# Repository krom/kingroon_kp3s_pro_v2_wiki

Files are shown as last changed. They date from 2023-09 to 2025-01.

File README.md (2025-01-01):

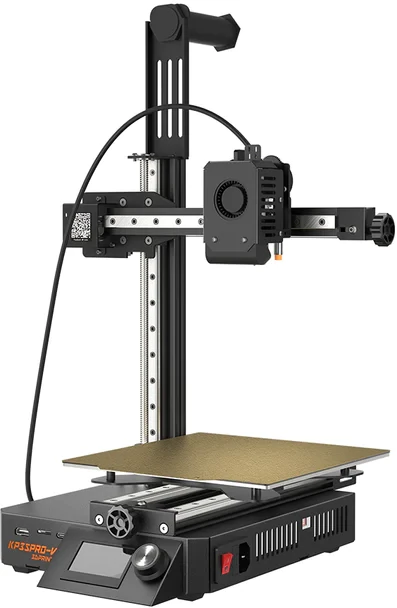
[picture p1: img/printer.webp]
Printer

# База знаний по принтеру Kingroon KP3S Pro V2 [RU]

* [Мануалы](manuals)
  * [SSH доступ](manuals/ssh_ru.md)
  * [Настройка wifi на принтере](manuals/wifi_connection_setup.md)
  * [Подключение к принтеру через сериальную консоль](manuals/serial_console_connection_ru.md)
  * [Обновление версии fluidd](manuals/fluidd_update_ru.md)
* [Известные проблемы](known_issues)
  * [Пластиковые проставки под платой на голове](known_issues/MKS_THR_Spacers_ru.md)
  * [Недостаточно затянутое сопло](known_issues/Nozzle_not_tight_ru.md) 
  * [Торчащие внутри балки X винты](known_issues/stick_out_screws_in_bolster_ru.md)
  * [Штатная улитка обдува не регулирует мощность](known_issues/Blowing_power_cannot_be_ajusted_ru.md)
  * [Проблема с упором головы по оси X](known_issues/x_offset_ru.md)
  * [Перевернутая скоба натяжителя ремня](known_issues/Inverted_tensioner_bracket_ru.md)
  * [Неправильные настройки шагов экструдера](known_issues/rotation_distance_ru.md)
  * [Не отображается карта стола](known_issues/fluidd_not_show_mesh_ru.md)
* [Советы по печати](tips)
  * [Клей](tips/Printing_glue_ru.md)
* [Апгрейд](upgrade)
  * [Улитка обдува](upgrade/Blower_ru.md)
  * [Хитблок от CHC](upgrade/CHC_ru.md)
  * [Установка датчика окончания филамента](upgrade/filament_runout_sensor_ru.md)
  * [Направляющая для кабеля стола](upgrade/bed_cable_guide_ru.md)
  * [Проставка между двигателем и фидером](upgrade/spacer_between_motor_and_feeder_ru.md)
* [Ремонт](repair)
  * [Прошивка платы головы из принтера](repair/How_to_flash_THR_Board_from_printer_ru.md)

# Kingroon KP3S Pro V2 Wiki [EN]
* [Manauls](manuals)
* [Known issues](known_issues)
  * [Nozzle is not tight](known_issues/Nozzle_not_tight_en.md) 
* [Tips and tricks](tips)
* [Upgrade](upgrade)
  * [Enable Filament Run Out Detection](upgrade/filament_runout_sensor_en.md)
* [Repair](repair)

----
[Группа в Telegram](https://t.me/kingroon_printers/384212)

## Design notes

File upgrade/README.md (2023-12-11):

# Апгрейд [RU]
* [Улитка](Blower_ru.md)
* [Хитблок от CHC](CHC_ru.md)
* [Установка датчика окончания филамента](filament_runout_sensor_ru.md)
* [Направляющая для кабеля стола](bed_cable_guide_ru.md)
* [Проставка между двигателем и фидером](spacer_between_motor_and_feeder_ru.md)
* [Замена заводской антенны WLAN](wlan_antenna.md)

# Upgrade [EN]
* [Enable Filament Run Out Detection](./filament_runout_sensor_en.md)

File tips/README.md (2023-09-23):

# Советы по печати
* [Клей](Printing_glue_ru.md)

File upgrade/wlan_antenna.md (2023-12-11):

## Замена антенны WLAN

Заводская антенна WLAN (она-же WI-FI) на принтере имеет довольно слабый прием. Дело в том, что ее реализовали в виде наклейки (та, которая с названием модели) на металлическом корпусе.
Близость металлического корпуса не способствует качеству приема:
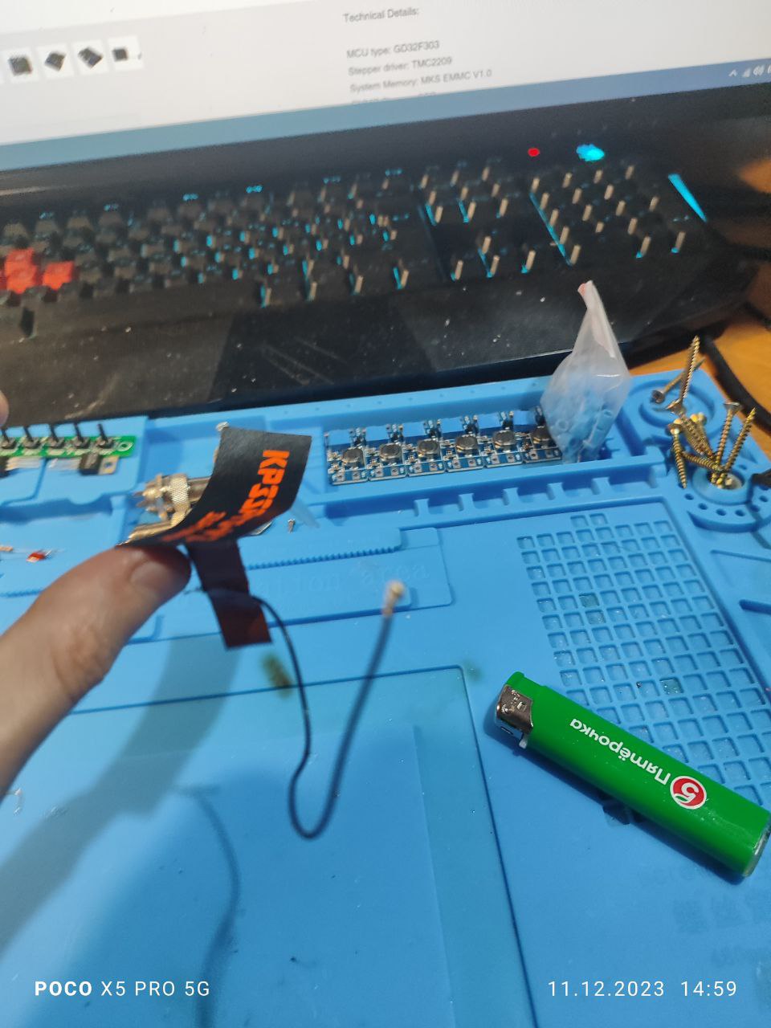
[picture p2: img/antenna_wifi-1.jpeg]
заводская антенна

Поскольку антенна подключена через стандартный разьем типа IPEX, можно заменить ее на что-то более чуствительное, например на внешнюю антенну от ESP32 типа такой:
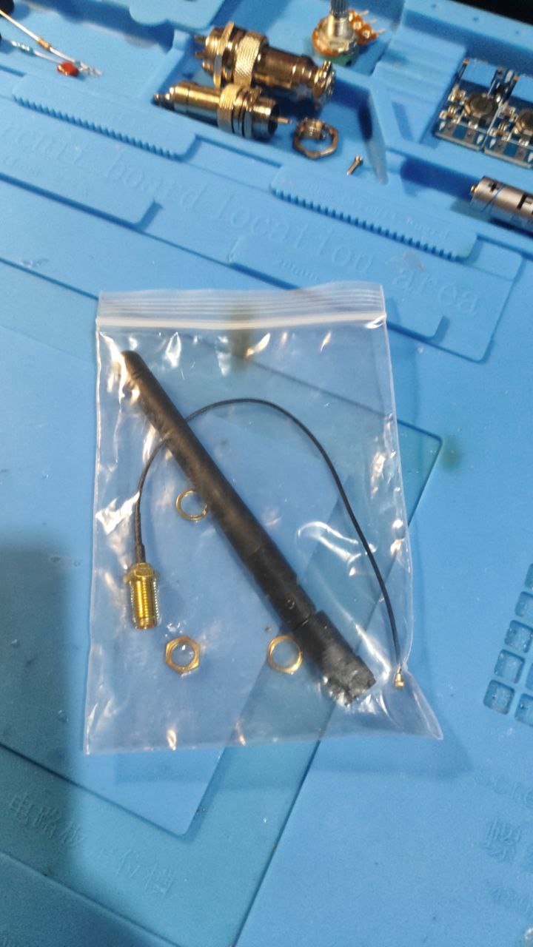
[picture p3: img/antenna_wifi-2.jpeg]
антенна ESP

Нужна антенна поддерживающая 2.4 Mhz и имеющая разьем [типа IPEX](https://en.wikipedia.org/wiki/Hirose_U.FL)
Т.е. отдираем наклейку - под ней стандартное круглое отверстие, через которое проходит кабель антенны к плате 
Отключаем старую антенну, заменяем на новую и перестаем мучаться, что принтер постоянно теряет связь с вашим домашним роутером:
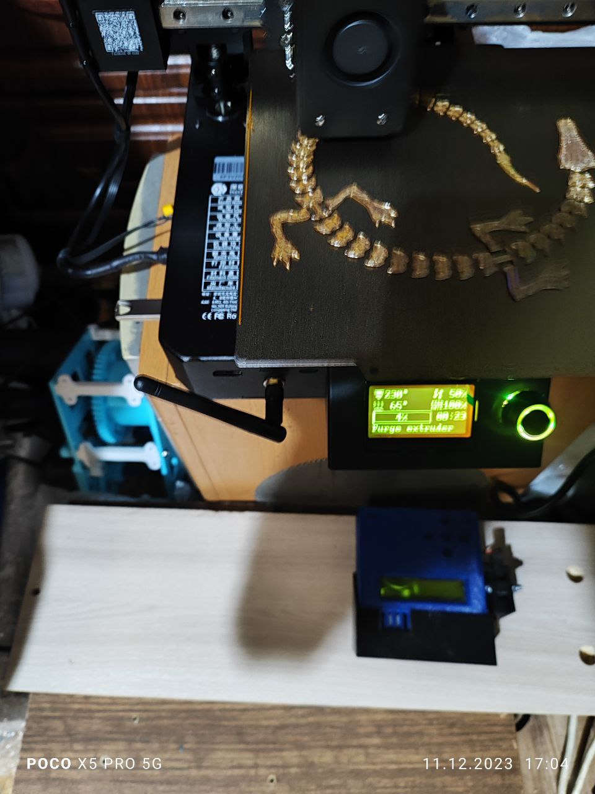
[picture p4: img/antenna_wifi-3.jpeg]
новая антенна


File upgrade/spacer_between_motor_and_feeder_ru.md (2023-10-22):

# Проставка между мотором и фидером

Шестерня двигателя не полностью пересекается с шестерней фидера и последняя может быстрее изнашиваться

Рекомендуется распечатать и установить проставку для выравнивания шестерней

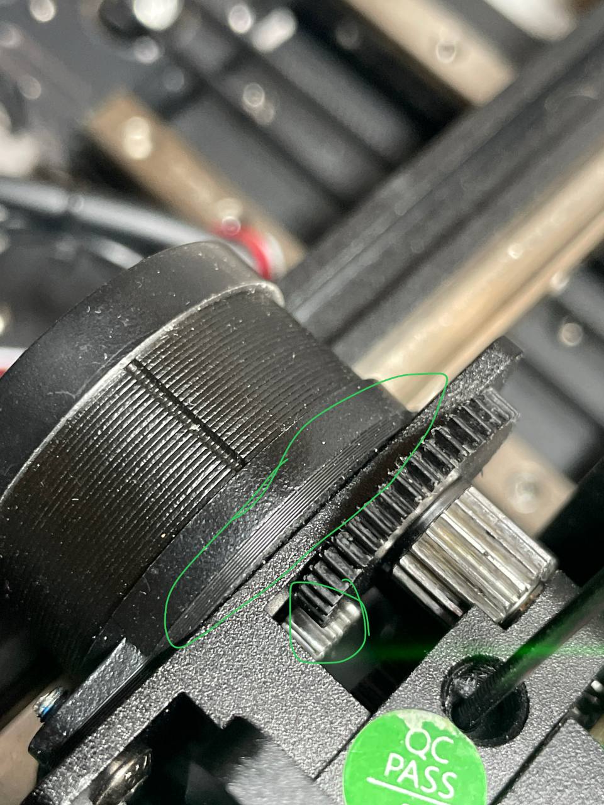
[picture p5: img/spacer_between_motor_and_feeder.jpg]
Spacer


## Доработка

1. Скачать [файл проставки с Printables](https://www.printables.com/model/566505-nema-14-junta-kp3s-pro-v2)
2. Распечатать деталь из PLA, лучше PETG
3. Открутить 2 винта крепления двигателя (для удобства лучше снять кожух головы)
4. Установить проставку как показано на изображении выше
5. Собрать голову в обратном порядке

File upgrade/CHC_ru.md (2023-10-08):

# Установка CHC или CHC pro

## Первые ревизии

В зависимости от того какая ревизия принтера у вас, стоковый хитблок можно заменить на более качественный от CHC/CHC Pro от Trianglelab

#### На версию с экраном под стоковый обдув подходит [CHC](https://alii.pub/6smfm6)

<div style="width: 60%; height: 60%">

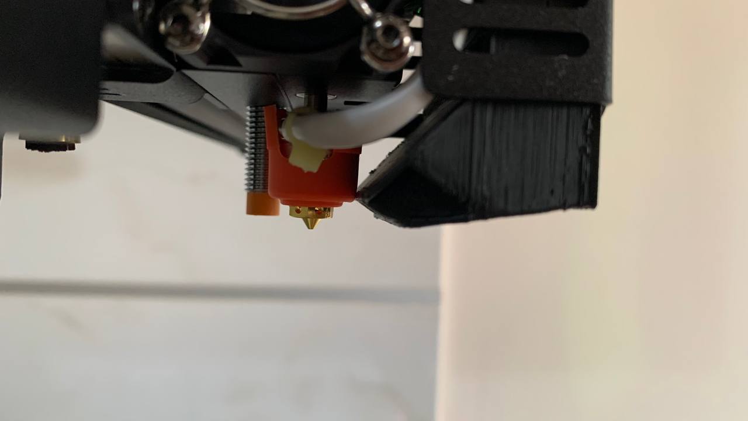
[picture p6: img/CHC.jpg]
CHC


</div>

#### На версию без экрана под стоковый обдув подходит [CHC Pro](https://alii.pub/6smfmk)

<div style="width: 60%; height: 60%">

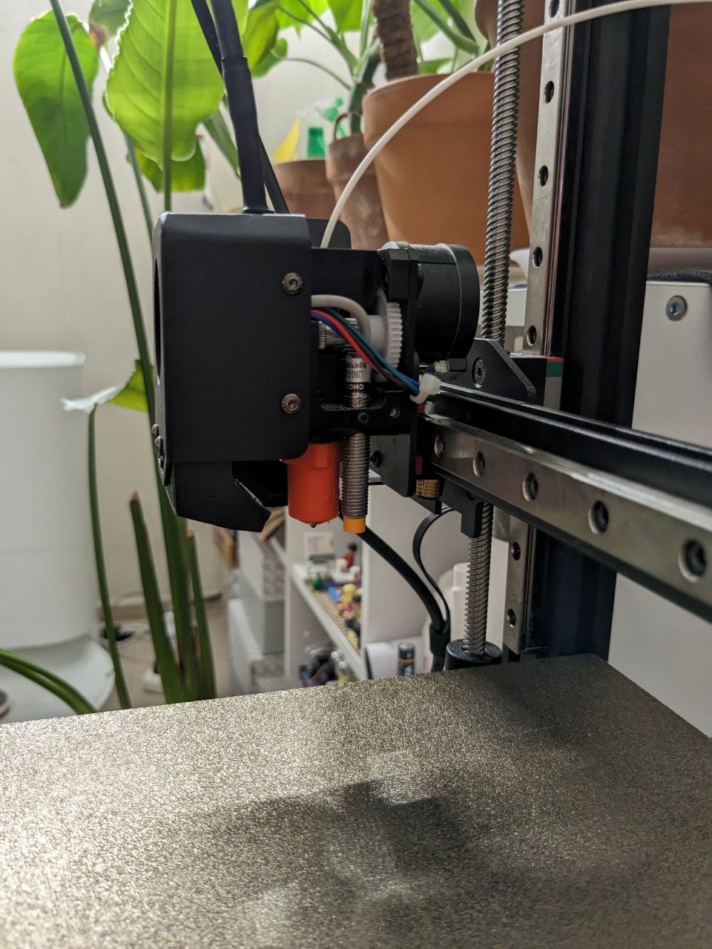
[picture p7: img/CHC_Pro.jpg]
CHC Pro


</div>

В обоих случаях используется горло длинной 25 мм, можно использовать либо стоковое, либо
* от [V5 ANYCUBIC Vyper](https://alii.pub/6sksir) - Если у вас **6 мм горло** и версия принтера без экранчика
* от [3DSWAY V6](https://alii.pub/6skskb) - Если у вас **7 мм горло** и версия принтера с экранчиком

> Проверяйте заранее диаметр горла перед тем как заказывать замену

## Более новые ревизии

В последних ревизиях принтера конструкция хитблока значительно изменилась. Теперь хитблок и горло составляют единое целое. В этих ревизиях заменить хитблок на CHC не представляется возможным

<div style="width: 60%; height: 60%">

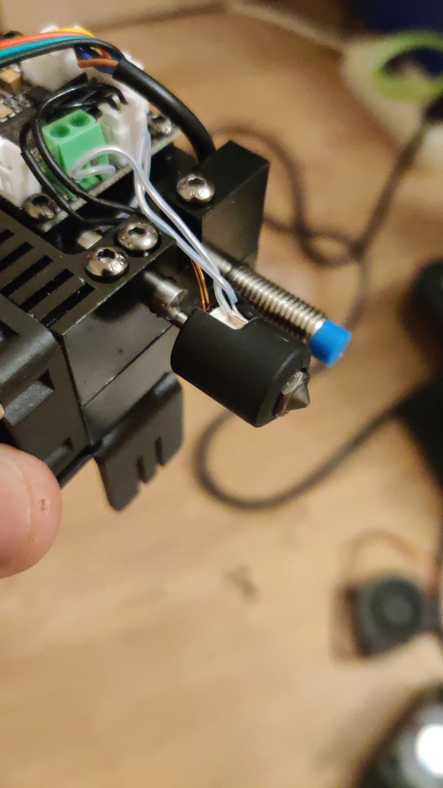
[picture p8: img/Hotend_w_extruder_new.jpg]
Hotend_w_extruder_new


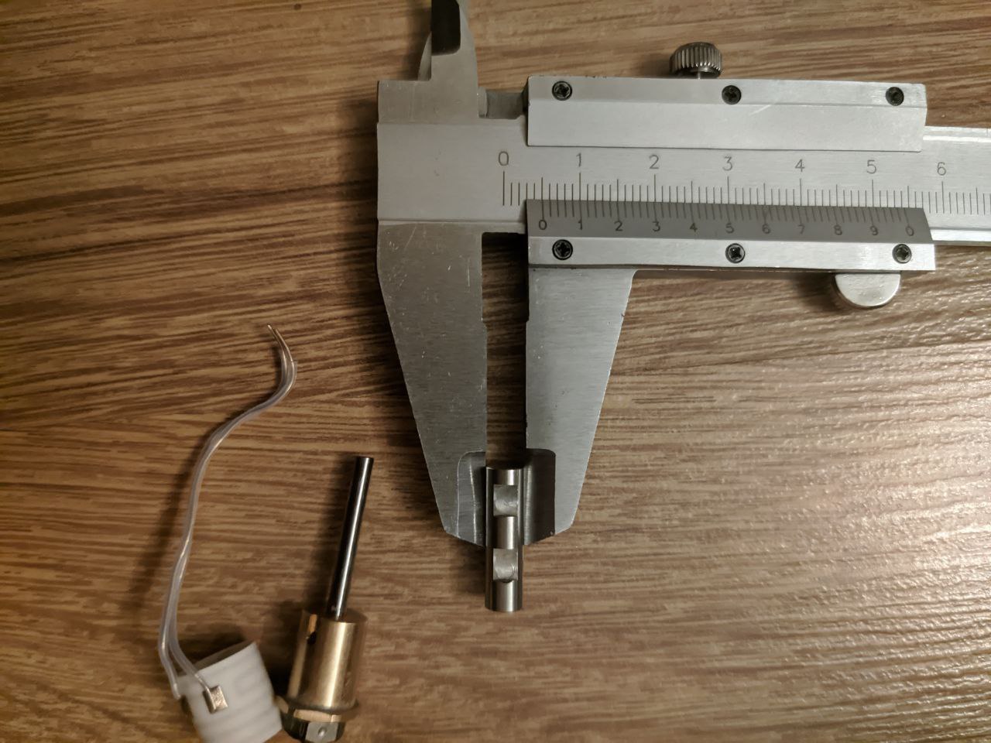
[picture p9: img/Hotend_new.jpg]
Hotend_new


</div>

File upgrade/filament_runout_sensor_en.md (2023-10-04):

# Enable Filament Run Out Detection

> Original post [here](https://kingroon.com/blogs/3d-print-101/enable-filament-run-out-detection-on-your-kingroon-kp3s-pro-v2-in-5-minutes)

The printer does not have a filament end sensor out of box, however, it can be easily installed separately

## Step 1
First you need to purchase the Ender 3 CR10 3D Printer Filament Break Detection Module

* [Official website](https://kingroon.com/products/3d-printer-filament-detection-sensor)
* [AliExpress](https://alii.pub/6sjr66)

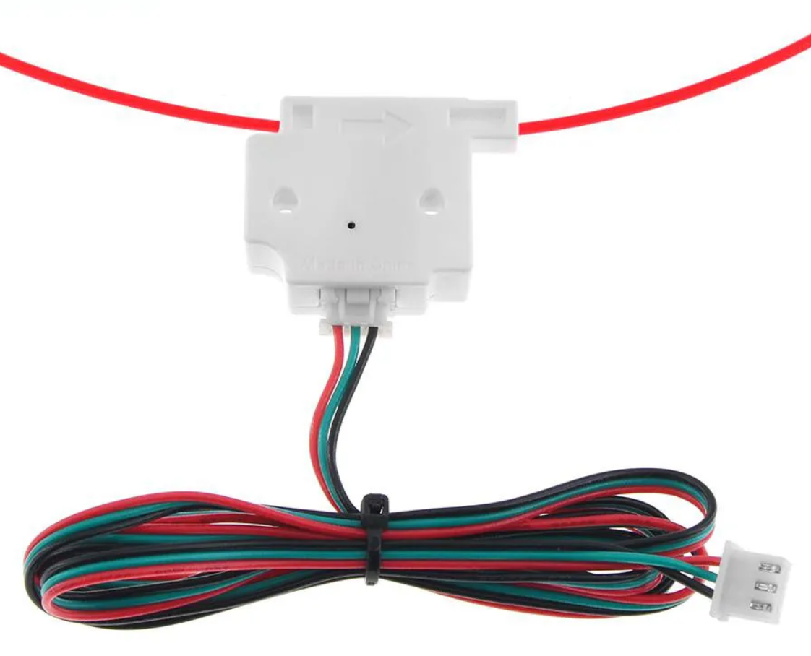
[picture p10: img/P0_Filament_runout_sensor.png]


## Step 2
Turn off the printer, remove the bottom cover then connect the filament run out sensor to the **PA1** port.

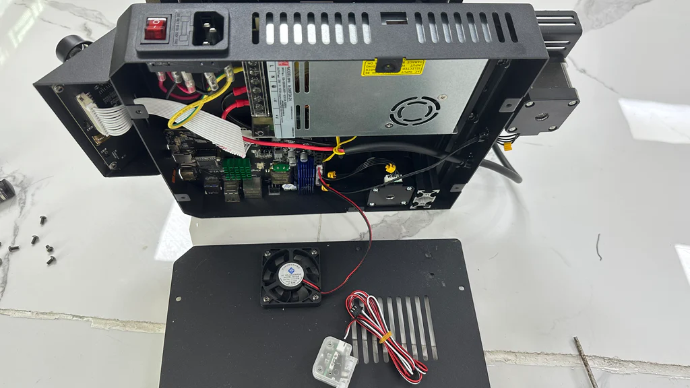
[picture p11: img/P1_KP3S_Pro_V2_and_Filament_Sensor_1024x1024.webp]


Go to the Y-axis motor, put the cable in through the hole near it.

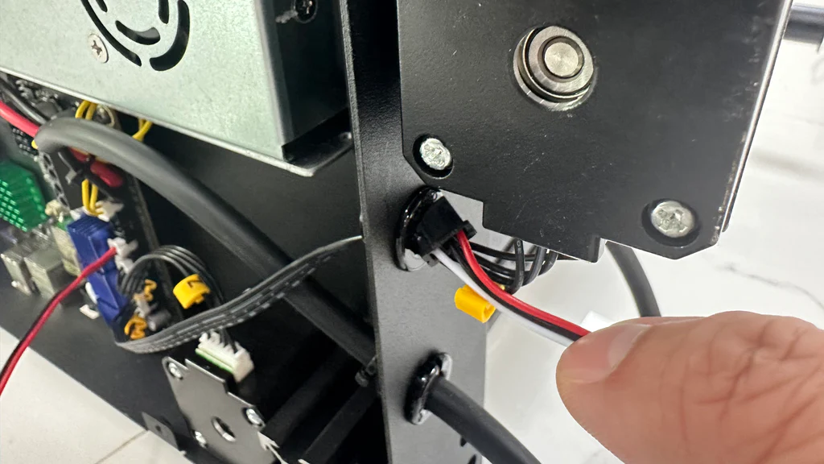
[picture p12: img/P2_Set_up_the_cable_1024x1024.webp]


Then connect the it to the **PA1** port and use some zip to fix it.

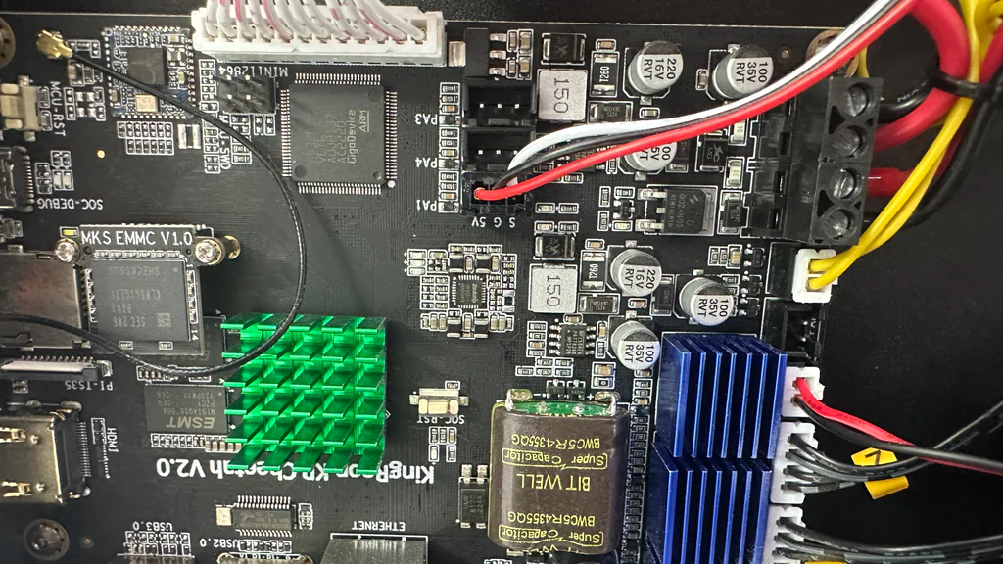
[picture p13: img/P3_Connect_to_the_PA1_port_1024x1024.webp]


After that you can put everything back and arrange the cables.
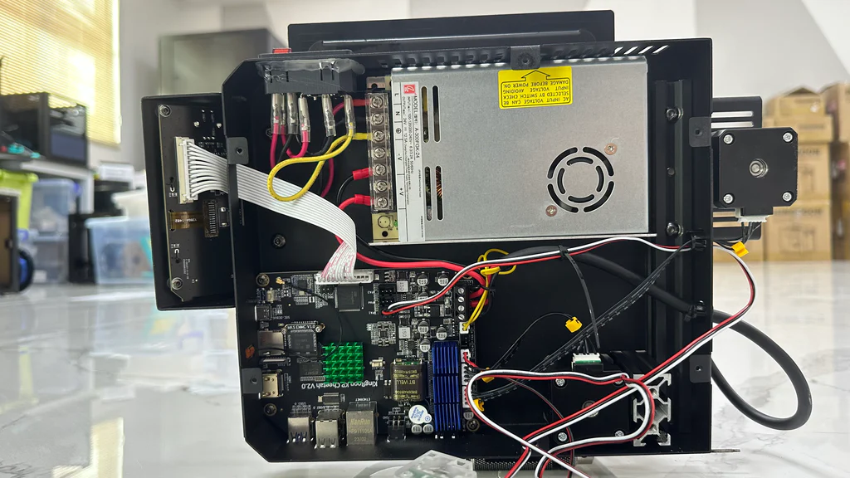
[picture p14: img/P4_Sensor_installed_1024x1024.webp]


## Step 3

Arrange the cables and install the sensor. The filament sensor has a cable that is over 1 meter, you need to fix it with the current ones to make it won’t cause any troubles.

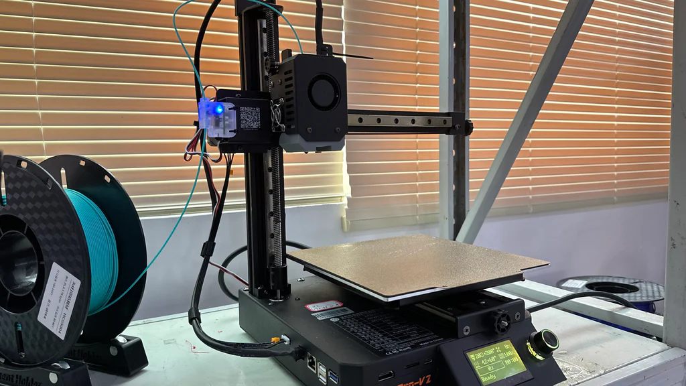
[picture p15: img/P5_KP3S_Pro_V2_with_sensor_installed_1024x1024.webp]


Then you can install the filament sensor with screws on the left side, like a KP3S Pro S1, or at the top of Z-axis. For the second way, you better get one print to make the filament guide smoothly. Since the KP3S Pro V2 prints in high speed, fixing it with ZIP won’t be enough.

Once you turn on the printer and insert the filament, the sensor should be on blue light. So, when the filament runs out on your KP3S Pro V2, the printing will be paused. After adding the filament, you can go the Klipper dashboard to resume it.

Since it is Klipper and our system images are updating, the resume printing might be automagical soon.

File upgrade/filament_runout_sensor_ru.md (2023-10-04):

# Установка датчика окончания филамента

> Оригинал статьи [тут](https://kingroon.com/blogs/3d-print-101/enable-filament-run-out-detection-on-your-kingroon-kp3s-pro-v2-in-5-minutes)

Принтер, не имеет датчика окончания филамента, однако, его можно легко установить отдельно

## Шаг 1
Для начала нужно приобрести Модуль обнаружения разрыва нити 3D-принтера Ender 3 CR10

* [Официальный сайт](https://kingroon.com/products/3d-printer-filament-detection-sensor)
* [AliExpress](https://alii.pub/6sjr66)



## Шаг 2
Выключите принтер, снимите нижнюю крышку, затем подключите датчик окончания нити к порту **PA1**



Ввод кабеля оптимальнее выполнить около мотора оси Y, проденьте кабель через отверстие возле него.



Затем подключите его к порту **PA1** и зафиксируйте с помощью пластиковой стяжки.



После этого можно собирать все обратно и подключать отключённые кабели.


## Шаг 3

Датчик имеет кабель длиной более 1 метра, его необходимо закрепить к сущ. кабелям, чтобы не возникало проблем.



Вы можете установить датчик с помощью винтов с левой стороны, как у KP3S Pro S1, или вверху оси Z. Для второго способа лучше напечатать подставку, чтобы направляющая нити шла плавно. Поскольку KP3S Pro V2 печатает с высокой скоростью, крепления с помощью пластиковых стяжек будет недостаточно и крепить лучше на винты.

Как только вы включите принтер и вставите филамент, датчик должен загореться синим светом. Таким образом, когда в KP3S Pro V2 закончится филамент, печать будет приостановлена. После добавления филамента нужно перейти в панель управления Klipper, чтобы возобновить печать.

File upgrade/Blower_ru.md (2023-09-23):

# Улитка обдува

Штатная улитка очень громкая и не умеет регулировать обороты - либо слабо, либо 100%

Рекомендуется сразу же заменить на что-то типа этого
* [Подороже, но тише](https://www.ozon.ru/product/ventilyator-5015-12v-gdstime-radialnyy-ulitka-s-sharikopodshipnikami-dual-ball-828114165/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)
* [Подешевле, но попроще](https://www.ozon.ru/product/933032956/?avtc=1&avte=2&avts=1695473214&sh=i03j4rB2rg)

### Важно
Под новые вентиляторы надо распечатать новый обдув, т.к. штатная улитка имеет нестандартные размеры

Скачать файлы можно по [ссылке](https://www.printables.com/model/531258-fan-duct-kp3s-pro-v2-with-display)

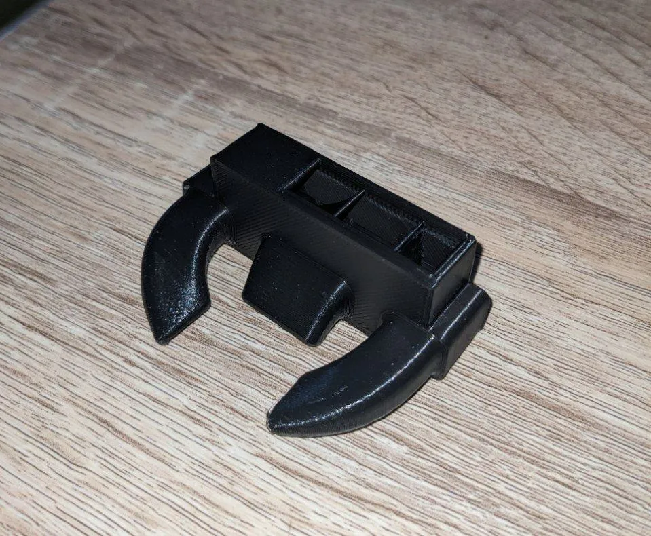
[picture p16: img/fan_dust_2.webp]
Изображение


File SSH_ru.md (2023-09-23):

# SSH Доступ к принтеру

Подключите принтер одним из двух способов

* Проводом
* По WiFi

Определить IP адрес можно одним из 3 способов

1. В самом принтере
2. В настройках вашего роутера
3. При помощи сканеров сети

### Параметры подключения
* Имя пользователя: mks
* Пароль: makerbase
* Root права: через sudo

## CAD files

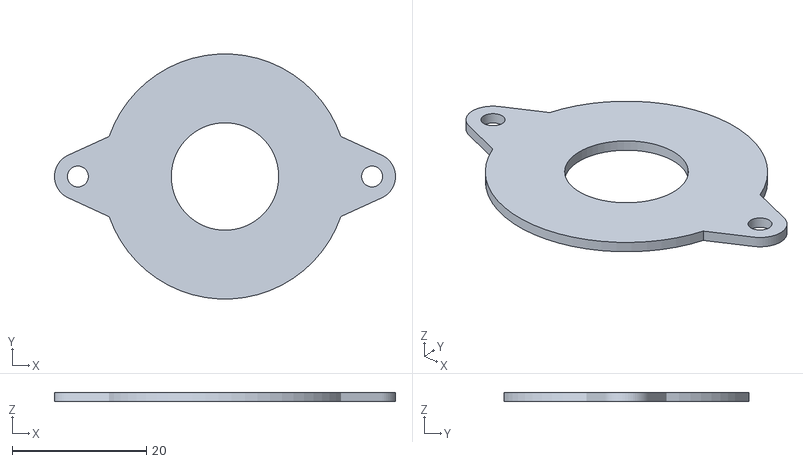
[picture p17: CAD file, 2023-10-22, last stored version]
files/nema-14-junta-kp3s-pro-v2-14mm.stl
50.9 x 36.5 x 1.40

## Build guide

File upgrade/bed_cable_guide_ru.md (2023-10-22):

# Направляющая для кабеля стола

Принтер имеет конструктивную проблему и кабель, который подходит к столу, может быть поврежден в процессе работы

Issue

Чтобы это не произошло, рекомендуется распечатать и установить направляющую
Guide

## Доработка
1. [Скачиваем файл с Printables](https://www.printables.com/model/511425-kingroon-kp3s-pro-v2-bed-cable-guide)
2. Находим 2 болта с гайкой на M3
3. Распечатываем и прикручиваем направляющую как показано выше

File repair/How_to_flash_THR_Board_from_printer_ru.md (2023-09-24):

# Прошивка платы головы с принтера

Основано на [оригинальной статье](https://kingroon.com/blogs/3d-print-101/flash-thr-board-firmware-of-kingroon-kp3s-pro-v2-klp1-3d-printer)

## Когда может пригодиться

В случае сбоя или при замене оригинального чипа RP2040 на купленный в стороннем магазине

## Что требуется

1. Принтер с ssh доступом
2. Рабочая плата головы
3. SSH клиент

## Действия

### 1. Подключаем голову и включаем принтер

* Полностью собираем голову
* Соединяем ее кабелем с принтером
* Включаем принтер и загружаемся

### 2. Переводим голову в режим bootloader
* Зажимаем кнопки reset и boot
* Отпускаем кнопку reset, boot продолжаем жать
* Через несколько секунд отпускаем кнопку boot

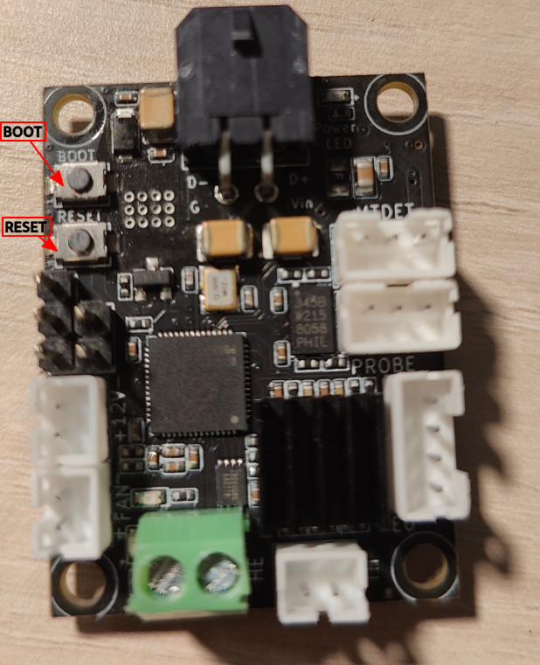
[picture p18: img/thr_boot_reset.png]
THR
* 

### 3. Заходим на принтер по SSH

> Далее есть 2 способа: автоматический и ручной

#### 3.1 Автоматический

**Данный скрипт пока в процессе разработки!**

~~curl -sL https://t.ly/FecEn | sudo bash~~

Далее вводим пароль от пользователя mks

#### 3.2 Ручной

Выполните следующую команду

```shell
lsusb
```

TBD

Вы должны увидеть следующий текст. Это значит, что плата головы успешно вошла в режим загрузчика и видится принтером

```shell
sudo su
wget https://github.com/krom/kingroon_kp3s_pro_v2_wiki/raw/main/files/klipper.uf2
mkdir /mnt/head/
mount -t vfat /dev/sda1 /mnt/head/
cp klipper.uf2 /mnt/head/
sync
umount /mnt/head
```

Вы должны получить следующее сообщение
```
umount: /mnt/head: not mounted.
```
Это правильно, плата головы получила прошивку и отключилась самостоятельно

### 4. Перезагрузите Firmware или принтер

Нажмите кнопку Firmware restart в веб интерфейсе клиппера или просто перезагрузите принтер
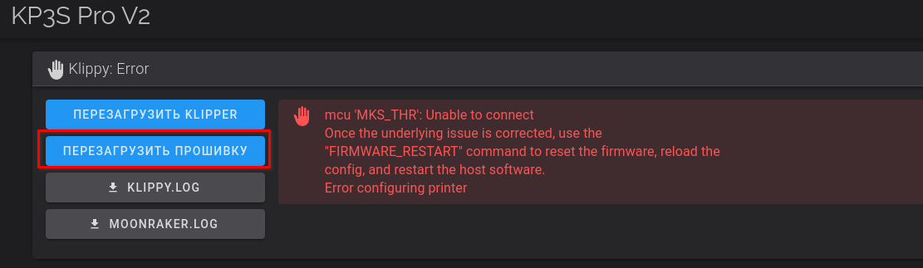
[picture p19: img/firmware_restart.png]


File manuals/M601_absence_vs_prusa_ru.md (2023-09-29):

# отсутствие поддержки G-codes M601,M602 в klipper

Если вы пользуетесь PrusaSlicer и вам необходимо печатать детали с "вложениями" (магниты, твердые вкладки,гайки и т.п.),
то в этом слайсере есть поддержка вставки паузы в процесс печати. Вы нарезаете в слайсере модель с внутренними полостями для вставок,
далее указывете на слое,который будет закрывать полость, что нужна пауза и в G-код будет вставлена команда M601, означающая, что принтер приостановит
печать чтобы вы положили в модель магнитик (или что-то еще). M601 - это стандартный код для этой самой паузы. 
Для возобновления печати достаточно дать команду M602.
К сожалению, несмотря на настройку в Prusaslicer "тип G-кода"=Klipper, пауза там реализуется только с помощью команды g-кода "M601".
Оказалось, что на принтере данный код не поддерживается (возможно, что это особенность настроек клиппера для KP3S Pro V2). 
Для klipper же введена команда 'PAUSE', которая как раз-таки поддерживается! Та-же проблема с командой M602.
К счастью это легко можно исправить. Нужно добавить в printer.cfg пару новых макросов:
```
[gcode_macro m601]
description: Pauses the current print.
  Usage: M601
gcode:
  PAUSE
[gcode_macro m602]
description: Resumes the currently paused print.
  Usage: M602
gcode:
  RESUME
```

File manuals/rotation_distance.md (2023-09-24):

# Настройка шагов экструдера (Rotation distance setup)
В настройках с фабрики стоит неправильное количество шагов - 43.7
Это неправильная настройка! 
Реально нужно поставить 53.6 
Неправильное кол-во шагов ведет к переэкструзии - филамента давится  +23% к потоку (давилось заместо 100мм прутка 123мм). 
Данные настройки нужно сделать в printer.cfg в разделе extruder:
```
[extruder]
rotation_distance: 53.6
```

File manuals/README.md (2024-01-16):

# Manuals
* [Шпаргалка по настройке Z offset](z_offset_quick_howto_ru.md)
* [SSH доступ](ssh_ru.md)
* [Подключение к принтеру через сериальную консоль](serial_console_connection_ru.md)
* [Настройка wifi на принтере](wifi_connection_setup.md)
* [Синхронизация времени на принтере](time_sync_ru.md)

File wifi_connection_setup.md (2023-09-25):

# Настройка wifi на принтере
Вторая ревизия принтера(которая с экранчиком) имеет встроенную wlan карту. У этой карты есть свои ограничения
 - К сожалению карта работает только на 2.4 Mhz.
 - Антенна очень скромная и наклеена к металлическому корпусу принтера - прием wifi у принтера оставляет желать лучшего...

Настроить linux подключаться к вашей точке доступа очень просто:

1. нужно иметь отформатированный под fat32 usb flash диск ( можно свой, а можно взять комплектный, который шел с принтером)
2. на диске нужно создать файл wpa_supplicant-wlan0.conf со следующим содержимым:
```
country=GB
ctrl_interface=DIR=/var/run/wpa_supplicant GROUP=netdev
update_config=1

network={
    ssid="Y0UR_P3RF3CT_ACC3SS_P0INT"
    psk="Y0ur_v3ry_s3cure_passw0rd"
    key_mgmt=WPA-PSK
}
```
3. отредактировать этот файл, нужно поменять ssid на название вашей точки доступа и psk на пароль к вашей сети wifi
4. вставить эту флэшку в один из usb портов принтера, включить принтер - и вуаля - принтер подключиться к вашей сети
5. на экранчике можно посмотреть какой ip адрес получил принтер, нажав крутилку, а на usb свистке появиться файл ip.txt
c этим же ip адресом
6. если все получилось - флэшка больше не нужна и ее можно убрать

комплектная флэшка уже правильно отформатирована и на ней есть готовый файл wpa_supplicant-wlan0.conf, который достаточно 
просто отредактировать

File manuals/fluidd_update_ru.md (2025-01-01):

# Обновление версии Fluidd

Fluidd - это web интерфейс принтера который стандартно показывется если набрать в web browser: **http://<printet_ip_adress>**

## Автоматическое обновление при помощи скрипта

1. нужно [зайти на принтер с помощью ssh](../manuals/ssh_ru.md)

2. Выполнить команду
```bash
curl -sL http://bit.ly/3ZX8mN0 | bash
```

## Ручное обновление
1. нужно [зайти на принтер с помощью ssh](../manuals/ssh_ru.md)
2. переименовать директорию, в которой стоит текущий fluidd, например командой:  
```bash
mv fluidd fluidd.bak
```

3. заново создать директорию fluidd и перейти в нее:

```bash
mkdir fluidd;cd fluidd
```

4. загрузить последнюю версию fluidd:

```bash
wget -q -O fluidd.zip https://github.com/fluidd-core/fluidd/releases/latest/download/fluidd.zip
```

5. распаковать архив fluidd.zip, затем опционально можно удалить сам архив:

```bash
unzip fluidd.zip
rm fluidd.zip
```

6. чтобы новая версия fluidd стала доступна, нужно перестартовать web сервер (nginx):

```bash
sudo service nginx restart
```

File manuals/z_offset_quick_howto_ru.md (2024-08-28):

## Небольшая шпаргалка по последовательности настройки уровня стола
Перед тем, как запускать калибровку сетки уровня стола необходимо провести калибровку Z_offset.
# небольшая теоретическая часть:

**fluid** - это веб интерфейс (web UI) на 80 tcp порту принтера. на него можно попасть настроив сеть на принтере. 

**Z_offset** - это расстояние от сопла до стола, когда срабатывает датчик автоуровня.

В Pro V2 используется индуктивный датчик уровня стола. Этот датчик срабатывает в 2 мм от поверхности металла.
В случае с принтером Kingroon KP3S Pro V2 поверхность металла это стальная пластина PEI.

**Внимание:** Очень важно всегда класть лист PEI перед любой калибровкой оси Z! Именно датчик выступает как концевик остановки
головы принтера по оси Z!

# Сама последовательность:
1. Проверяем что датчик автоуровня находится по оси Z выше сопла, но не более 2 мм. **Если эта величина окажется больше 2 мм - сопло будет при 
   калибровке давить в стол и перекосит балку оси X!!!**
   Идеально 1.5 - 1.8 мм - если нет - поправляем ослабляя винт крепления датчика. Делается это на отключенном принтере. 
3. Убеждаемся, что балка оси Y стоит параллельно столу. Это можно сделать сдвинув голову и стол, так чтобы голова была где-то посредине стола.
   Далее простой линейкой замеряем расстояние от балки до стола в начале и конце балки - это расстояние должно быть одинаковым.
   Если это не так - путем небольшого ослабления винтов крепления балки можно ее подровнять. Это тоже делается на отключенном принтере.
4. Настраиваем сеть на принтере (если это еще не сделано)
5. Заходим на принтер по сети на web интерфейс и прогреваем стол до температуры, на которой обычно идет печать(допустим 60 градусов)
   Можно прогреть стол на +5 градусов больше. Сопло должно быть чистым - никаких остатков пластика на нем не должно быть.
6. Выбираем на FLUID web ui в макросах “calibrate Z_OFFSET”  кнопку и жмем (там вместо слова 'calibrate' могут быть китайские иероглифы и это не шутка)
   Принтер переводит голову в центр стола и по оси Z выше стола где-то на мм 10-15 и на на web интерфейсе появляется новое окошко с диалогом 
   калибровки.
7. Берем лист офисной бумаги  и кладем под соплом.
8. Кнопками в диалоговом окне _медленно_ опускаем сопло до тех пор, пока сопло не прижмет лист бумаги.
   При этом лист должен быть прижат, но с небольшим усилием можно будет двигать под соплом.
   Хотя присутствуют кнопки опускания и поднимания головы на разные величины, желательно, чтобы голова только опускалась до прижатия соплом листа 
   бумаги
9. В диалоговом окне жмем 'save Z_offset - принтер перегружает процессы клиппер и сохраняет значение Z_offset.
10. значение z_offset сохраняется в файле printer.cfg
 ближе к концу примерно так:
```
#*# [probe]
#*# z_offset = 0.325
```
11. Далее можно совершенно спокойно идти в web ui на раздел tune и проводить  bed mesh calibrate -
    **не забудьте** сохранить полученный результат в профиле default. Опять-таки эта сетка сохраняется в файле printer.cfg в конце.

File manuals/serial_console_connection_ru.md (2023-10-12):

# Подключение к принтеру через сериальную консоль
Для различных диагностических и конфигурационных целей есть возможность подключиться к основной плате принтера по сериальной консоли:
1. нужен кабель type-C <-> type-A
2. кабель одним концом втыкается в порт type-C принтера - другой стороной - в USB порт вашего компьютера
4. на компьютере принтер будет выглядеть как usb2serial устройство CH340 (USB VID 0x1a86 PID 0x7523) и должен появиться новый сериальный порт(в windows
  COM?: , в Linux /dev/ttyUSB?, в macos /dev/tty.usbserial???). Для операционной системы windows возможно потребуется [установка драйверов CH340](https://www.google.com/search?q=windows+ch340+driver+download)

5. на компьютер нужно будет поставить какую-нибудь терминальную программу. Например для windows: putty, secureCRT. Для linux или macos - minicom, tio или screen
6. подключаемся к порту c помощью терминальной программы, параметры соединения speed 1500000,no parity, 1 stop bit. должны также отрабатывать скорости 115200,38400
7. Если все сделано правильно - то после нажатия  enter в терминале должен появиться запрос логина и пароля linux

эта полноценная консоль - на нее в том числе выводиться сообщения от загрузчика (bootloader) и собствено сами сообщения ядра linux

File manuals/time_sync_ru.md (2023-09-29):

# Синхронизация времени на принтере

На основной плате нет батареи, поддерживающей RTC (real-time clock) это означает, что время на принтере при старте linux будет выставлено

на момент, когда принтер был выключен. Из-за этого принтер с фабрики показывет время на момент апреля 2023 года.

Это крайне неудобно, например для отладок, просмотра журналов и т.д.  по какой-то причине синхронизация времени на принтере в armbian не настроена. Причина в том, что синхронизация 

с помощью systemd-timesyncd.service, который по включен в автозагрузку, блокируется установленным ntpd, а автостарт ntp.service конфликтует с systemd-timesyncd.service.

Для того, чтобы на linux время было актуальным необходимо сделать следующие шаги:

1. зайти на [linux по ssh](ssh_ru.md) или [на консоль](serial_console_connection_ru.md)

2. настороить таймзону:

*   дать команду 
``` bash
sudo armbian-config 
```
* в появившемся меню выбрать Personal -> Timezone -> Europe -> Moscow (либо другую,  подходящую вам временную зону

3. отключить конфликтующий сервис systemd-timesyncd.service: 

``` bash
sudo systemctl disable systemd-timesyncd.service
```

4. убедиться , что сервис ntpd прописан в автозагрузку:

```
sudo systemctl enable ntp.service
```

5. дать команду на старт ntpd и убедиться что он стартовал и стал синхронизировать время с серверами ntp:

```
sudo systemctl start ntp.service
sudo systemctl status ntp.service
date
```

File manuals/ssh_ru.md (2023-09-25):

# SSH Доступ к принтеру

Подключите принтер одним из двух способов

* Проводом
* [По WiFi](wifi_connection_setup.md)

Определить IP адрес можно одним из 4 способов

1. В самом принтере
2. В настройках вашего роутера
3. При помощи сканеров сети
4. В файле `ip.txt` в корне USB флешки после подлючения к WiFi

### Параметры подключения

| Параметр | Значение |
|---|---|
| Имя пользователя | mks |
| Пароль | makerbase |
| Root доступ | Имеется через sudo |

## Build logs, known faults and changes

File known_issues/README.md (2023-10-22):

# Известные проблемы [RU]

* [Пластиковые проставки под платой на голове](MKS_THR_Spacers_ru.md)
* [Недостаточно затянутое сопло](Nozzle_not_tight_ru.md)
* [Торчащие внутри балки X винты](stick_out_screws_in_bolster_ru.md)
* [Штатная улитка обдува не регулирует мощность](Blowing_power_cannot_be_ajusted_ru.md)
* [Проблема с упором головы по оси X](x_offset_ru.md)
* [Перевернутая скоба натяжителя](Inverted_tensioner_bracket_ru.md)

# Know issues [EN]
* [Nozzle is not tight](Nozzle_not_tight_en.md)

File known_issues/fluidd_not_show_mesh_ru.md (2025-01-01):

## Проблема отображения сетки стола

По сообщениям некоторых пользователей последние сборки прошивок принтера имеют проблему:
**Не отображается профиль высот стола стола в web интерфейсе fluidd!** Кроме этого может не отображаться 
предпосмотр g-code. 
Fluidd - это web интерфейс принтера который стандартно показывется если набрать в web browser: **http://<printet_ip_adress>**
Существует несколько решений данной проблемы:
- откатиться на более старую версию прошивки - профиль высот гарантированно работает в прошивке "armbian-KP3S Pro V2-20230606"
- использовать другой web ui интерфейс - во всех версиях прошивки присутствует и работает второй по популярности интерфейс к Klipper - Mainsail
Для доступа к mainsail web ui нужно набрать в строке web browser **http://<printet_ip_adress>:81**
- если принтер может выходить в internet,то можно обновить fluidd до последней версии [по инструкции](../manuals/fluidd_update_ru.md)

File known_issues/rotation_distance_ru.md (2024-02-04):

# Настройка шагов экструдера или rotation distance
Rotation distance - это расстояние в миллиметрах на которое переместится ось за одно полное вращение шаговика, т.е. за одно полное вращение шаговика принимается оборот на 360 градусов.

**В настройках с фабрики стоит неправильное количество шагов - `43.7`**
**Это неправильная настройка!!**
Неправильное кол-во шагов ведет к переэкструзии - филамента давится `+23%` к потоку (давилось заместо 100мм прутка 123мм). 

Идеально было бы провести калибровку количества шагов 
Методика того, как это можно сделать, описана например [здесь](https://klipper.wiki/ru/home/tuning/rotation#rotation_extruder) или [здесь](https://www.klipper3d.org/Rotation_Distance.html)
у автора этого текста получилась величина `53.6`, в принципе ею можно воспользоваться.

Данные настройки нужно сделать в `printer.cfg` в разделе `extruder`:
```
[extruder]
rotation_distance: 53.6
```

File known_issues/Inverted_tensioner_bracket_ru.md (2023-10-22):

# Перевернутая скоба натяжителя ремня

Скоба натяжителя на оси х и у имеет 2 отверстия. Одно с резьбой, второе почти без, что позволяет винту прокручиваться в нем . И изначально эти скобы установленны резьбой вниз (дальняя часть скобы от шляпки болта фиксирующего ролик ) из за этого при затягивании болта скоба сжимается и начинает тереть о ролик .
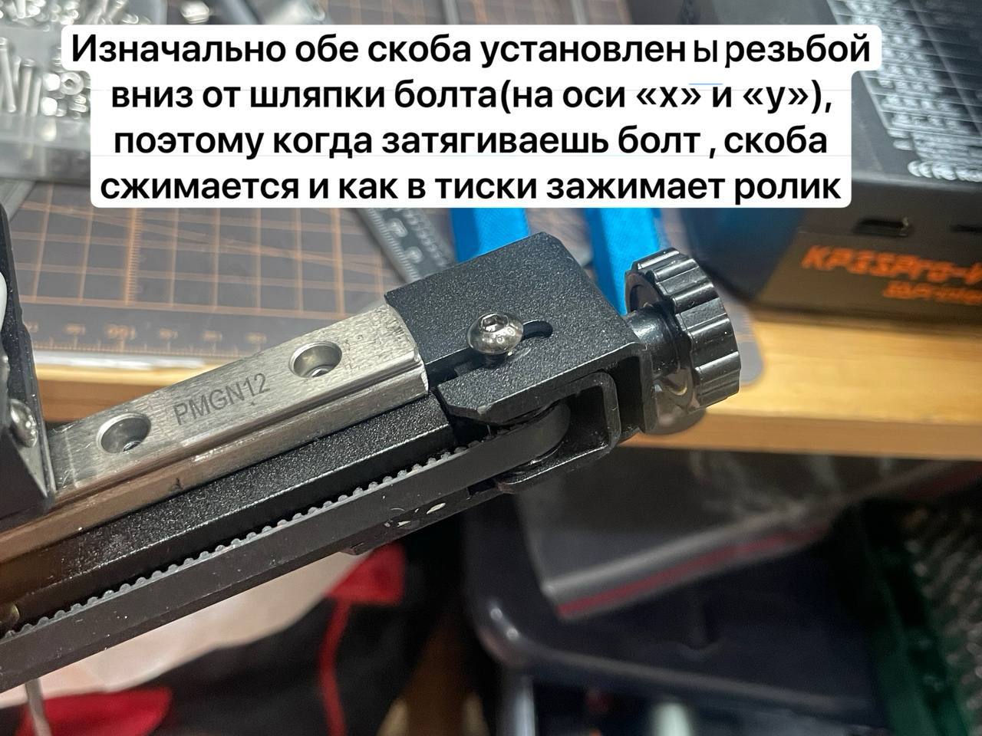
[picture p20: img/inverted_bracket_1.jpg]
inverted bracket 1


## Что предлагается сделать
- Выкручиваем винт натяжителя
- выкручиваем винт фиксирующий скобу
  - снимаем скобу
  - если уже перетягивали его, то исправляем геометрию скобы (плоскогубцами или руками)
- переворачиваем скобу так, чтобы резьба была ближе к шляпке болта.
- устанавливаем ремень с роликом
- наживляем винт (проверяем чтобы резьба была сверху у того места с короной вкручиваем винт)
- устанавливаем на место
- Закручиваем регулировочный барашек и натягиваем ремень.
- и теперь можно нормально затянуть винт фиксатора, не боясь погнуть скобу и не боясь заблокировать ролик .

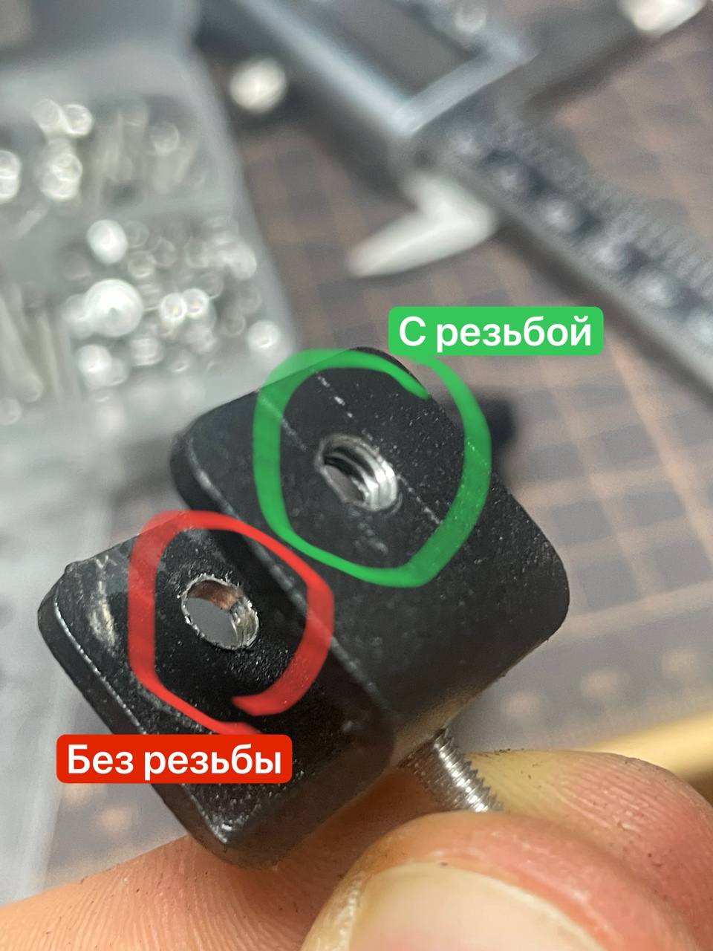
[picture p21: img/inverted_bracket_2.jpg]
inverted bracket 2

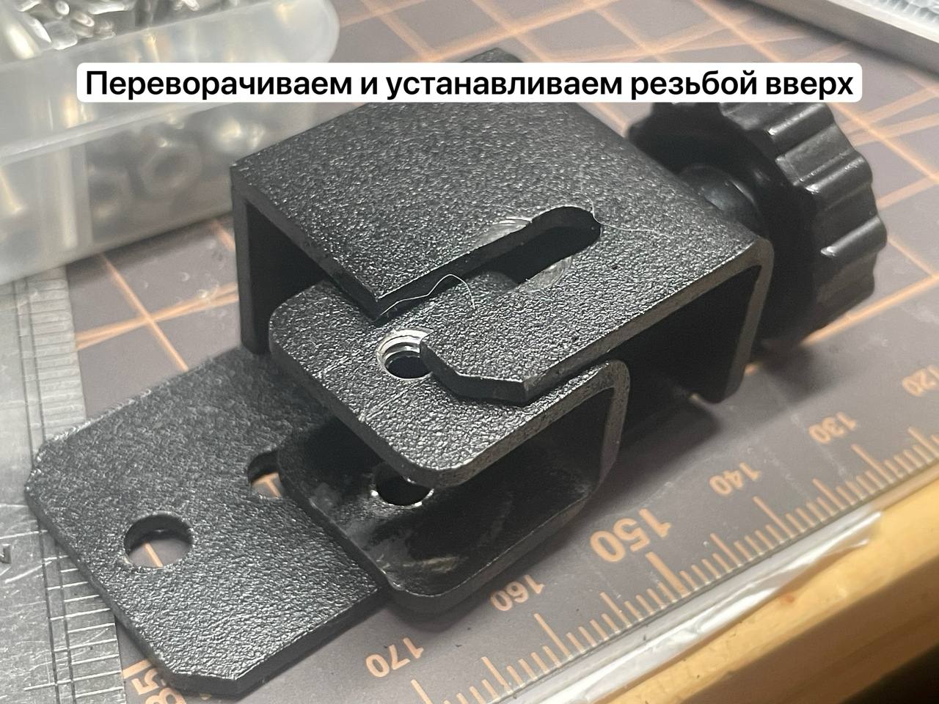
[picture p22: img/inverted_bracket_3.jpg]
inverted bracket 3

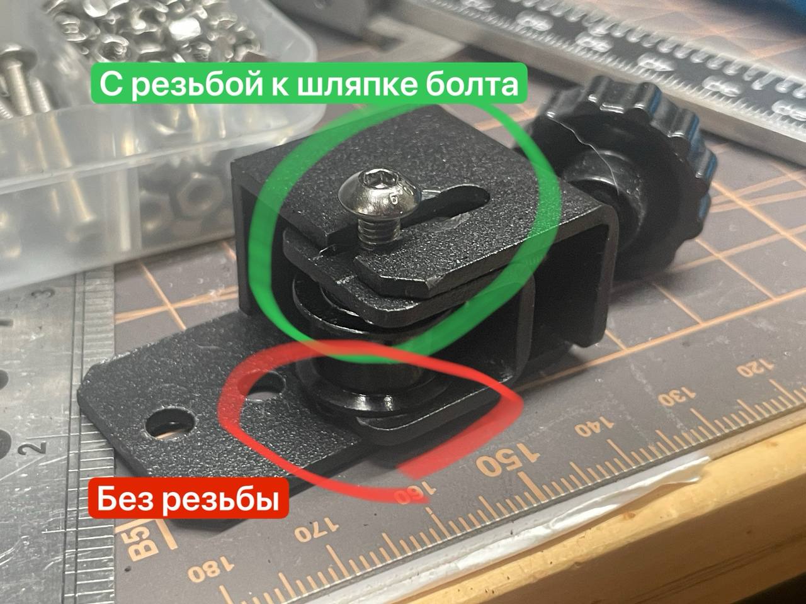
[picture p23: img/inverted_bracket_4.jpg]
inverted bracket 4


Спасибо [@kireevk](https://t.me/kireevk)

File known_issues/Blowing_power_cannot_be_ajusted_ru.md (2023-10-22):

# Штатная улитка обдува не регулируется

Штатная улитка очень громкая и не умеет регулировать обороты - либо слабо, либо 100%

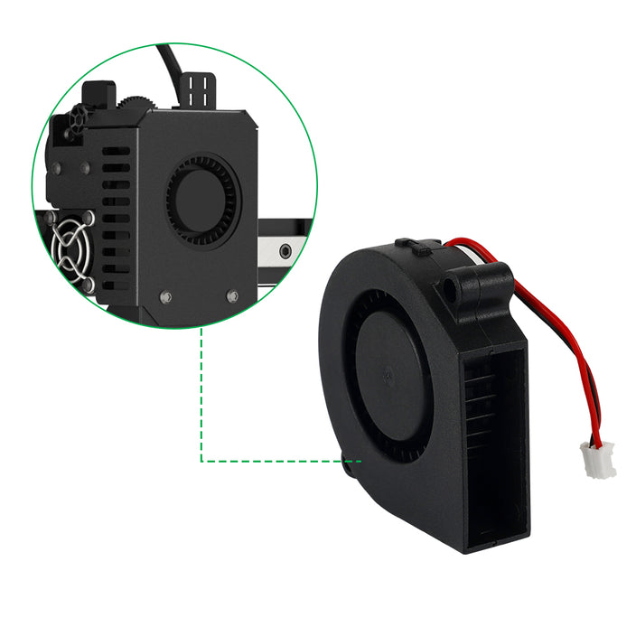
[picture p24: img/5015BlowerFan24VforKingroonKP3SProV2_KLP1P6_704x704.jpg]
Blower


Есть 2 варианта решения данной проблемы:
1. Покупка рабочей улитки с [официального сайта](https://kingroon.com/collections/kingroon-kp3s-pro-v2-replacement-parts-accessories/products/5015-blower-fan-24v-12v-for-kingroon-kp3s-pro-v2-klp1) - не проверялось
2. Установка другой улитки с заменой охлаждения [по инструкции](../upgrade/Blower_ru.md) - рекомендуется

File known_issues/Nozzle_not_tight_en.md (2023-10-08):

# Nozzle is not tight

Manufacturers periodically ship printers with insufficiently tightened necks and nozzles. This causes the plastic to flow under the ceramic ring and break it.

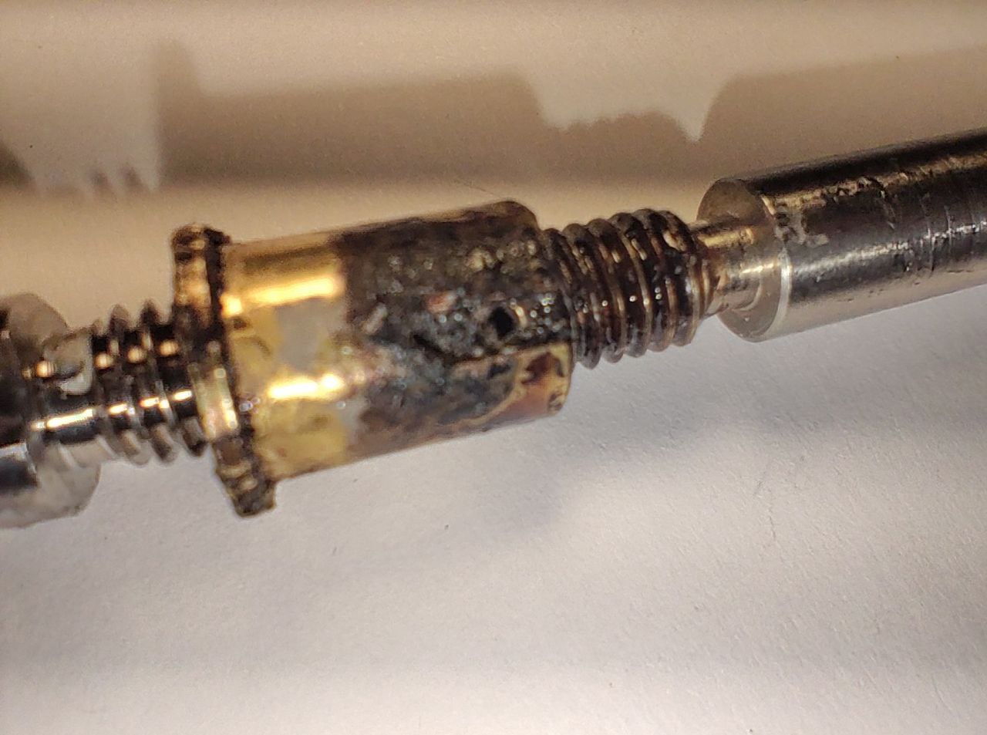
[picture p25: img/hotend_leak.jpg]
hotend_leak


Therefore, after purchasing a printer, it is worth tightening the nozzle to a hot one. You must be extremely careful when doing this, as the heating element is very fragile.

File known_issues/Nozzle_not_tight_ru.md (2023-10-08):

# Недостаточно затянутое сопло

Китайцы периодически страдают тем, что недостаточно затягивают горло и сопло. Это приводит к тому, что пластик затекает под керамическое кольцо и ломает его.

hotend_leak

Потому после покупки принтера стоит подтянуть сопло на горячую. При этом надо быть крайне аккуратным, так как нагревательный элемент очень хрупкий.

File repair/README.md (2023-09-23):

# Ремонт
* [Прошивка платы головы из принтера](How_to_flash_THR_Board_from_printer_ru.md)

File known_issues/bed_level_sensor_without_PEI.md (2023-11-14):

## Описание проблемы:
Будьте осторожны: **НЕ ПОСЫЛАЙТЕ ПРИНТЕР В Home Position/Парковку СО СНЯТЫМ ЛИСТОМ PEI!**
Результаты могут оказаться довольно неприятными - "голова" принтера может продавить датчиком стол, может нарушиться угол в 90 градусов между поперечной
балкой и осью Z, стол может изогнуться и т.д. 
В общем могут возникнут серьезные механические нарушения настроек принтера, которые потребуют времени на их устранения!

## Разьяснения и теория:
В принтере для измерения расстояния от печатающей "головы"  до стола используется **индуктивный датчик уровня**. 
Индуктивные датчики срабатывают от металлических поверхностей токопроводящих поверхностей. 
Особенностью модели датчика использованного в Kingroon KP3S PRO V2 является то, что он **срабатывает на расстоянии 2мм** 
от металлической поверхности. В нормальном режиме такой поверхностью выступает лист PEI, поскольку основой его является токопроводящая сталь.
При парковке голова принтера опускается по оси Z до тех пор, пока не сработает датчик. Т.о. датчик выступает в том числе и своеобразным концевым 
выключателем, ограничивающим положение 0 по оси Z.
Датчик не срабатывает на магнитный "резиновый" слой, т.к. этот слой слабо проводит ток. 
Магнитный слой имеет довольно большую толщину(более 2 мм), поэтому датчик не срабатывает от находящегося под ним алюминия стола.
В результате, если снять лист PEI и послать печатающую голову в позицию home, голова начинает опускаться, датчик упирается в магнитный слой, не срабатывет
голова продлжает опускаться в ниже уровня стола, соответственно вызывая те самые механические нарушения!
Другой "защиты от дурака" в принтере в данной ситуации не предусмотрено.
К сожалению заменить индуктивный датчик на какой-либо другой затруднительно - плата в печатающей голове (THR Board) на это
не рассчитана - например обычно используемый для таких целей BL touch датчик требует подключения по 5 проводам, 
в отличии от более примитивного индуктивного датчика. 

## Способы устранения, предупреждения:
Как оказалось, датчик реагирует на обычную алюминиевую пищевую фольгу. Предлагается прикрепить небольшой кусочек фольги в один слой поверх магнитного слоя, 
где датчик опускается в позиции home. 
Толщина пищевой фольги из алюминия варьируется от 8 до 12 микрон, поэтому этой величиной можно пренебречь - на геометрию стола подобное добавление 
сильно повлиять не должно, но заметно сбережет нервы забывчивых людей 😀

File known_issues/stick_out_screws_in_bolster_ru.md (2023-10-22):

# Торчащие внутри балки X винты
В принтере перемещение по оси X происходит при помощи ремня, закрепленного обоими концами на голове. 
Сама голова с всеми ее компонентами при этом скользит по рельсе, закрепленной на балке оси X. 
Верхняя часть ремня проходит через отверстие вдоль всей балки оси X, и с одной стороны балки выходит на шестеренку мотора, 
а с другой стороны проходит через натяжитель. 

Как выяснилось, производитель использовал слишком длинные винты, которыми вышеупомянутая рельса привинчена к балке. 
Их концы **торчат внутри** отверстия балки, и мешают свободно ходить расположенному внутри балки ремню, **цепляются за него**!   

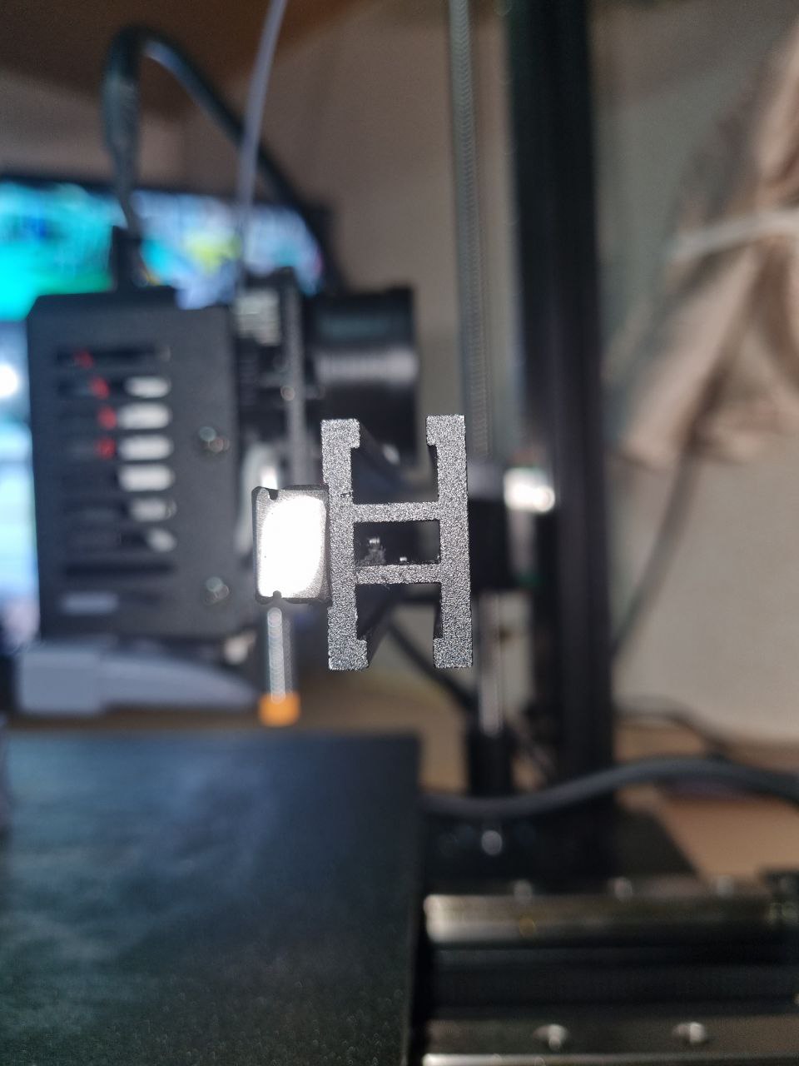
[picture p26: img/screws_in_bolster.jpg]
торчащие концы винтов


В результате концы винтов постоянно скребут по краю ремня, повреждая его и вызывая дополнительные вибрации головы принтера: 

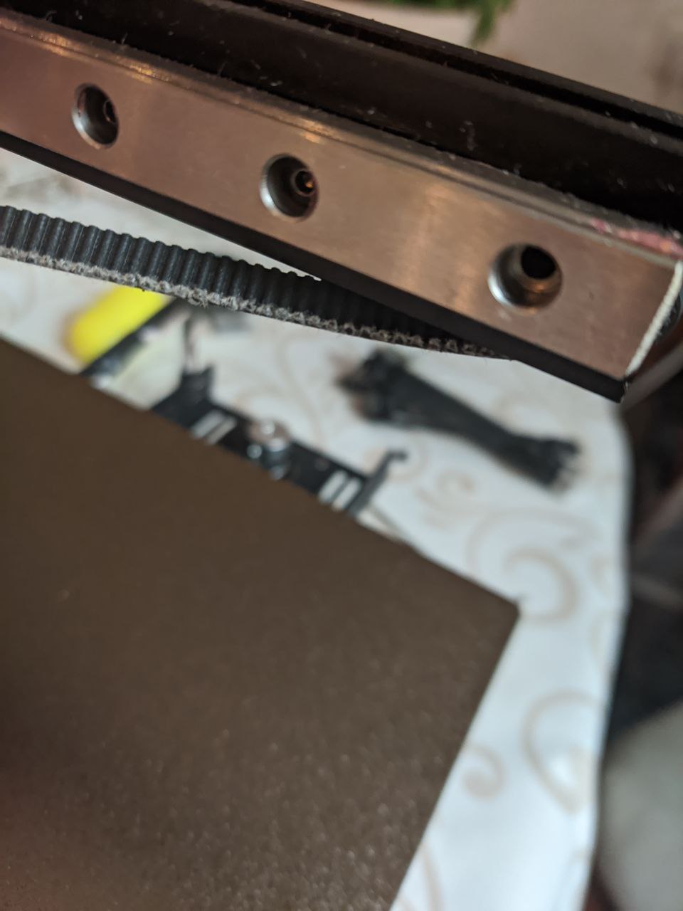
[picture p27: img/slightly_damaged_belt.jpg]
поврежденный ремень оси X


Для исключения данной проблемы можно либо немного укоротить длину винтов, либо заменить их на более короткие. 
Проблемные винты имеют длину резьбы 7.5 мм. Чтобы они не цепляли ремень нужно укоротить их примерно на 2 - 2.5 мм. Идеально, чтобы длина резьбы была 6 мм
Кроме этого рекомендуется проверить и заменить/укоротить, в случае излишней длины, два винта, которыми к балке оси X крепиться натяжитель.

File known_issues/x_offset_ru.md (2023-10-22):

# Проблема со стопором по оси X
В принтере вместо концевика используется датчик тока шагового двигателя когда подвижная часть упирается в неподвижную ответную часть

На балке оси X подразумевается, что балка с подшипниками упирается в скобу слева
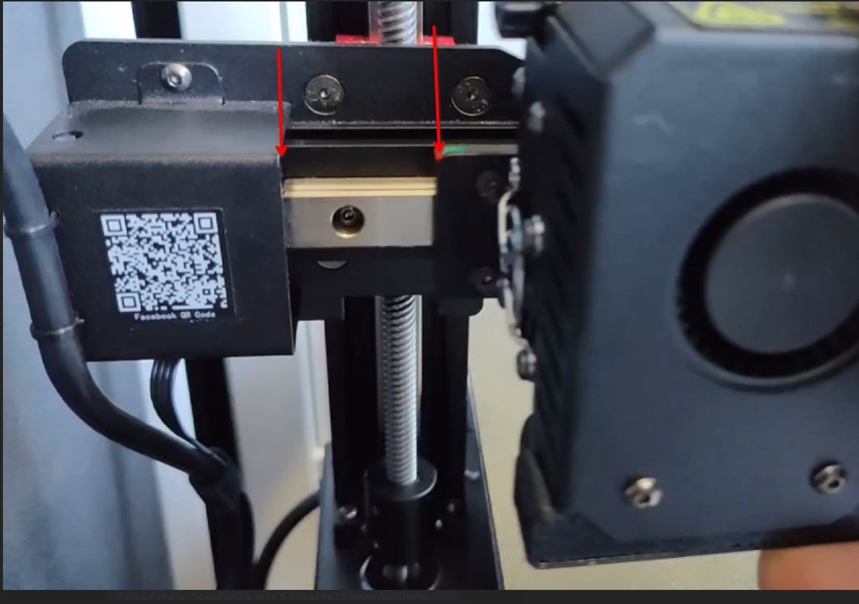
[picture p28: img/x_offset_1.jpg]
x offset 1

Однако, она может проскользнуть внутрь
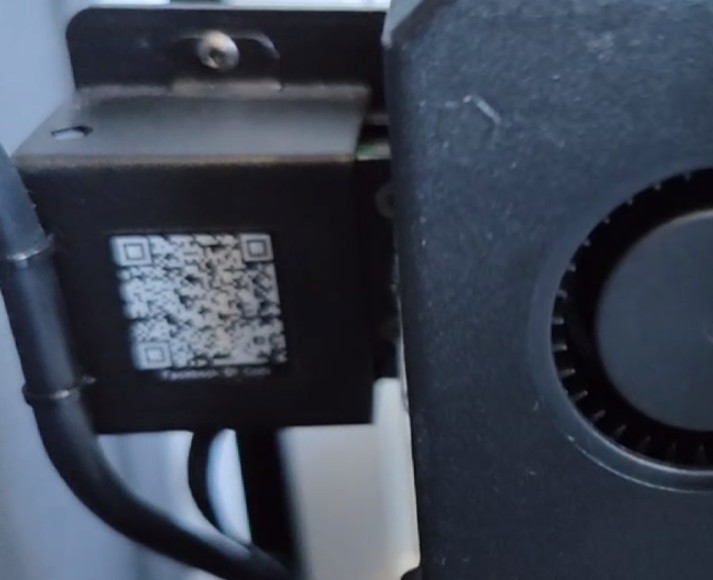
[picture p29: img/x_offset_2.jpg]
x offset 2


Чем это грозит:
1. Сдвиг оси X примерно на 10 мм, т.е. печать на 5 мм будет происходить в воздухе за пределами стола
2. Рельса выходит из балки и обнажаются подшипники, что может приводить к их засорению или даже выпаданию

Рекомендуется поставить дополнительный упор по типу такого
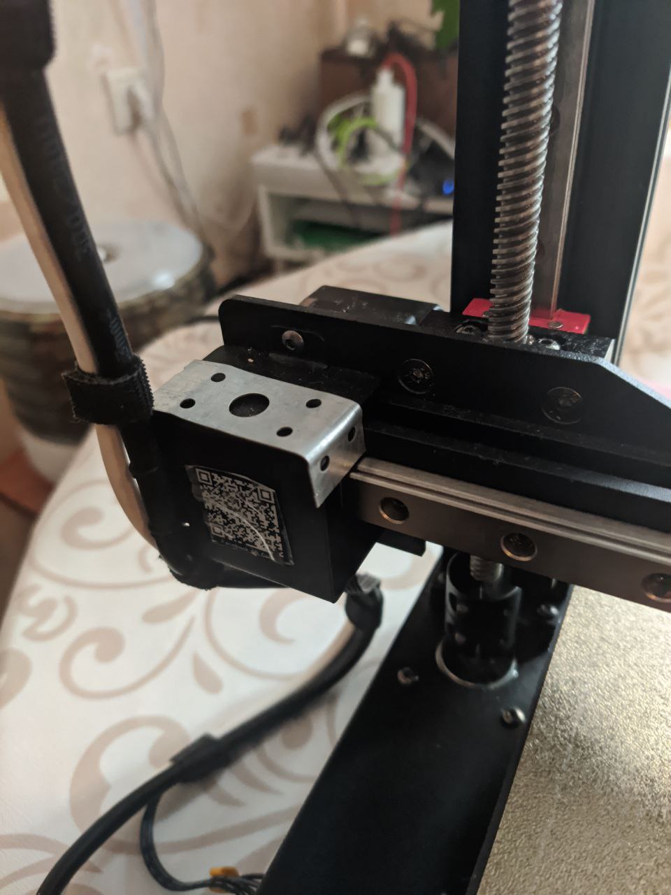
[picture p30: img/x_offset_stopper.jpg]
x offset stopper


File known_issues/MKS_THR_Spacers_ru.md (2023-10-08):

# Пластиковые проставки под платой на голове

При проектировании/сборке головы разработчики прогадали с размером проставок излориующих плату от экструдера. Это приводит к сдвигу диода шотки и обычно выходу из строя как платы головы, так и платы принтера

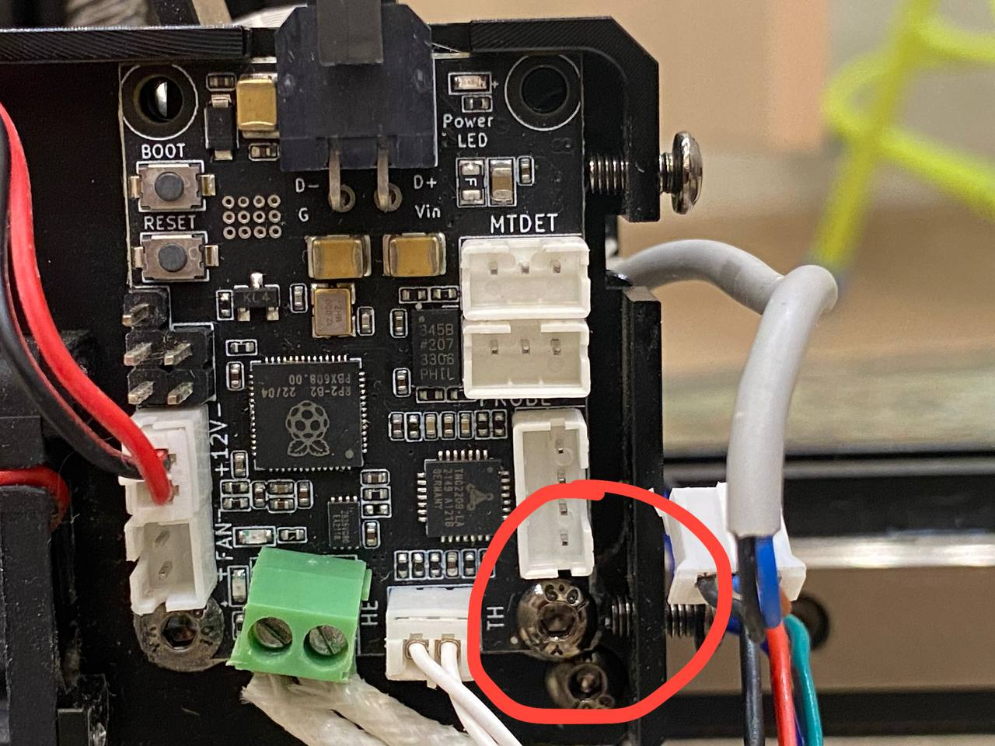
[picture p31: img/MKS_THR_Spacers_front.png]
Front View


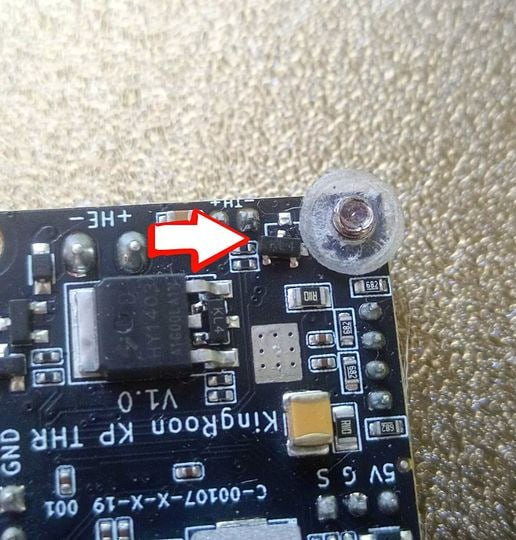
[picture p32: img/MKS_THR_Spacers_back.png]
Back View


> **Внимание!**
> Данная проблема наблюдается только на первых ревизиях головы, на актуальной этих проставок уже нет

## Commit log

2023-09-23 Added links to fan dust
2023-09-24 Настройка WIFI на принтере
2023-09-24 Update How_to_flash_THR_Board_from_printer_ru.md
    grammar nazy хочет добавить букву р
2023-09-24 Настройка шагов экструдера (Rotation distance setup)
2023-09-25 Create serial_console_connection.md
    доступ к принтеру через сериальную консоль
2023-09-25 updated photo of printer
2023-10-04 added filament runout sensor
2023-10-12 Update serial_console_connection_ru.md
    добавлена информация про необходимости установить драйвер CH340 на windows
2023-10-15 фото торчащих винтов в отверстии балки
2023-10-15 поврежденный винтом ремень оси X
2023-10-16 Update stick_out_screws_in_bolster_ru.md
    немного поправил грамматику
2023-10-22 added upgrade instructions
    [nema-14-junta-kp3s-pro-v2-14mm.stl]
2023-11-14 Create bed_level_sensor_without_PEI.md
    Индуктивный датчик не срабатывает на магнитный стол
2023-12-11 Create wlan_antenna.md
    новая антенна
2023-12-11 Update README.md
    добавлена новая статья в оглавление
2024-01-16 Create z_offset_quick_howto_ru.md
    добавлена шпаргалка по настройке z_offset
2024-02-04 Update rotation_distance_ru.md
    добавил немного теории и ссылки на методику калибровки шагов экструдера
2024-08-10 Update z_offset_quick_howto_ru.md
    поправил про расстояние от сопло до датчика
2025-01-01 Добавлена инструкция по обновлению fluidd
2025-01-01 Обновлена документация
2025-01-01 Обновлены скрипты
2025-01-01 Добавлен вспомогательный скрипт
